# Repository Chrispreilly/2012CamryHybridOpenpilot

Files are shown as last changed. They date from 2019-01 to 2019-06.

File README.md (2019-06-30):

Got a 2018 subaru, moving the forked OP to https://github.com/c-reilly/openpilot-2012camryhybrid

# 2012 Toyota Camry Hybrid Openpilot

### Openpilot Repo

https://github.com/chrispreilly/openpilot   

### Physical Components

##### Purchased / Standard Compenents
- EON
- (Grey) Panda
- Motor Controller Board
  - See MotorControllerWiring
  
##### Customized Components Needed
- Motor Mount & Steering Wheel Mount
  - See MotorMount example, need to customize this for each car
  
### Ignition
The Panda is plugged into the OBD port, and on my Toyota the ignition pin on the panda matches with the 12V supply. As a work around I've changed in thermald to sense ignition at 13V. Battery voltage is ~12.5V, so it only senses igniton when the car is on and inverter brings the voltage up to ~13.5V.

### CAN Communication - Required Messages  
I have all messages being sent over the OBD CAN bus. As long as the steering control and safety check messages don't conflict with nything in your car, you should be able to use the OBD bus.

##### Inputs from car to openpilot:
- Blinker
- Brake Pedal
- Gas Pedal
- Wheel Speed
- Steering Angle
- Cruis Control On/Off

##### Inputs from car to Motor Controller:
- Steering Angle

##### Inputs from Openpilot to Motor Controller:
- Desired Angle

##### Inputs from Motor Controller to Openpilot:
- CAN Safety Check

### Safety
- Belt Tension should never exceed what the driver can override
- Arduino sends a CAN check message every 100ms. If openpilot doesn't hear the message for 250ms it will disengage
- If Arduino sees a gap betwwen recieving Desired Angle from Openpilot or Current Angle from the car it will turn off the motor
- If Openpilot sees a delta between current angle and desired angl of >5 degrees (meaning user override or motor lost power) it will disengage

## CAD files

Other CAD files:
MotorMount.dwg
WheelMount.dwg

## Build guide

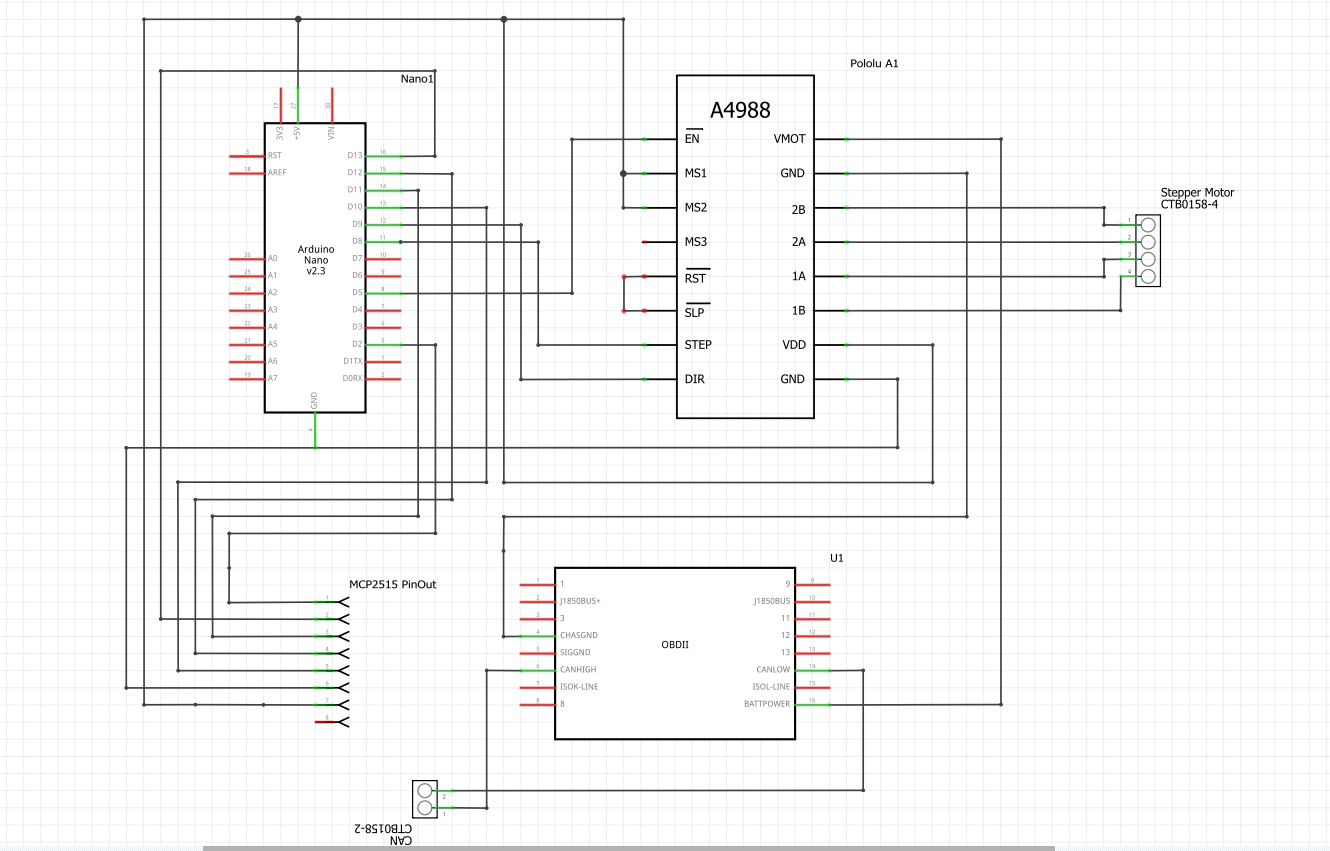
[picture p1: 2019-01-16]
MotorControllerWiring.PNG

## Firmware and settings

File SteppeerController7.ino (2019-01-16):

/*
 * Parts used
 * 
 * 1x Arduino
 * 1x MCP2515 CAN Transciever
 * 1x A4988 Stepper Driver
 * 1x NEMA17 stepper motor
 */



#include <AccelStepper.h>
#include <SPI.h>          //SPI is used to talk to the CAN Controller
#include <mcp_can.h>

//Stepper control with openpilot
//Set these variables for system config
double steerGear = 220; //steering gear diameter
double motorGear = 8; //motor gear diameter
//double angleError = 0; //degrees error needed to disengage
double microsteps = 4; //microstepping (1 = standard, 2 = half step, 4 = quarter step, 8  = eigth step)
int stepperSpeed = 2200;
int stepperAcceleration = 10000;

//set enable pin on A4988 driver
int enablePin = 5;

//init other variables
float gearRatio = 0;
float currentAngle = 0;
float desiredAngle = 0;
double lastDesiredAngle = 0;
double lastCurrentAngle = 0;
double angleDelta = 0;
double zeroAngle = 0;

long desiredStep = 0;
long lastDesiredStep = 0;
long currentStep = 0;

bool currentEngaged = false;
bool previousEngaged = false;
bool steerOverride = false;

double angleToStepFactor = 0;
double stepToAngleFactor = 0;
unsigned char len = 0;
unsigned char buf[8];
unsigned int canID;
unsigned char buf0 = 0;
unsigned char buf1 = 0;
unsigned char buf2 = 0;
unsigned char buf3 = 0;
unsigned char buf4 = 0;
unsigned char buf5 = 0;
unsigned char buf6 = 0;
unsigned char buf7 = 0;

float measure0 = 0;
float measure1 = 0;
float measure2 = 0;
float measure3 = 0;
float measure4 = 0;

int currentTime = 0;
int lastRequestTime = 0;
int lastReadTime = 0;
int lastGoToTime = 0;
int counter = 0;

float canCheck = 0;
unsigned char msg[2] = {0, 0};
int lastCANCheckTime = 0;


AccelStepper stepper(1, 8, 9); //(type(leave as 1 for a4988), step, direction)
MCP_CAN CANR(10); //CAN CS Pin



void steerCommandReceived() {
  //Serial.println("Update Received");

  //reads either 0 or 1
  buf0 = buf[0];
  currentEngaged = bitRead(buf0, 0);

  //combine 2 bufs to create big one
  buf1 = buf[1];
  buf2 = buf[2];
  measure1 = (buf1 << 8);
  measure2 = buf2;
  desiredAngle = measure1 + measure2;
  desiredAngle = desiredAngle / 100;

  lastRequestTime = millis();
  //Serial.println(desiredAngle);
  //Serial.println(currentEngaged);
  return;
}

void carAngleReceived() {

  buf0 = buf[0];
  buf1 = buf[1];
  buf4 = buf[4];
  measure0 = buf0;
  measure1 = buf1;
  measure4 = (buf4 >> 4);
  if (measure4 >= 8) {
    measure4 = -16 + measure4;
  }

  //if greater than 0, negative turn
  if (buf0 > 0) {
    currentAngle = -(384 - (measure1 * 1.5) - (measure4 / 10)); //15/16 converts to more accurate removed 15/16 because it seems more accurate to what OP is reading
  }
  else {
    currentAngle = (measure1 * 1.5) + (measure4 / 10); //15/16 converts to more accurate
  }


  //counter = counter +1;
  //Serial.println(counter);

  lastReadTime = millis();
  //Serial.print(measure1*1.5);
  //Serial.print("  ");
  Serial.println(currentAngle);
  //safetyCheck();
  return;
}

void safetyCheck() {

  return;
}

void disableLock() {
  //stepper.disableOutputs();
  //while (true){
  //delay(5000);
  //}
}

void updateDesiredStep() {

  
  angleDelta = desiredAngle - currentAngle;
  currentStep = stepper.currentPosition();

  //minus (-) because stepper is reversed direction
  desiredStep = currentStep - angleDelta * angleToStepFactor;  //currentStep + angleDelta * angleToStepFactor;
  //Serial.println(desiredStep);

//only update if reasonable change, need to determine a good number
  if (abs(lastDesiredStep - desiredStep) > 10) {

    lastDesiredStep = desiredStep;
    stepper.moveTo(desiredStep);
  }
  

  return;
}

void sendCANCheck() {

//CAN ID 500/0x1f4
  CANR.sendMsgBuf(0x1f4, 0, 2, msg);
  canCheck = canCheck + 1;
  msg[0] = canCheck;
  if (canCheck == 50)
  {
    canCheck = 0;
  }

  lastCANCheckTime = millis();

  //CANR.sendMsgBuf(0x512, 0, 2, msg); test
  //CANR.sendMsgBuf(0x513, 0, 2, msg);
  return;
}



void setup() {
  //set enable pin to disable immediately
  pinMode(enablePin, OUTPUT);
  digitalWrite(enablePin, HIGH);
  Serial.begin(115200);
  
  //Initialize CAN
RETRYCANONE:
  if (CAN_OK == CANR.begin(CAN_500KBPS))     //setting CAN baud rate to 500Kbps
  {
    Serial.println("CAN BUS Receive Shield init ok!");
    delay(5);
  }

  else
  {
    Serial.println("CAN BUS Receive Shield init fail");
    goto RETRYCANONE;
  }


//calculate system parameters
  gearRatio = motorGear / steerGear;

  stepToAngleFactor = (gearRatio) * (360 / 200) * (1 / microsteps);
  angleToStepFactor = 1 / stepToAngleFactor;

  //set stepper speed and acceleration - tune these to each system
  stepper.setMaxSpeed(stepperSpeed); //steps per second
  stepper.setAcceleration(stepperAcceleration);

  //stepper.setCurrentPosition(0);

}



/*
 * loop() updates current steering angle from the car, and desired angle from Openpilot. 
 * Based on the difference it calculates how many steps to move to achieve the desired angle and requests to move there.
 * It continues to update at 200hz as both current angle and desired angle changes.
 * Also takes advantage of the enable pin on the A4988 to disable the stepper when not engaged.
 * 
 */
void loop() {

  //Check for a new CAN message and read if angle read or request
  if (CAN_MSGAVAIL == CANR.checkReceive())
  {
    CANR.readMsgBuf(&len, buf);
    canID = CANR.getCanId();

    //If the ones we care about...
    if (canID == 0x2e4) //angle request & engaged
    {
      steerCommandReceived();
    }
    else if (canID == 0x25) //steering angle
    {
      carAngleReceived();
    }
  }



  //update MoveTo every 5 milliseconds
  currentTime = millis();
  if ((currentTime - lastGoToTime) > 5 ) { //(desiredAngle != lastDesiredAngle) && 
    //Serial.println("run");
    lastDesiredAngle = desiredAngle;
    lastGoToTime = currentTime;
    updateDesiredStep();
  }



  //enable outputs when engaged
  if (currentEngaged == true)  { // && previousEngaged == false) {
    digitalWrite(enablePin, LOW);
    previousEngaged = currentEngaged;
  }

  //disable outputs when disengaged
  else if (currentEngaged == false)  { // && previousEngaged == true) {
    digitalWrite(enablePin, HIGH);
    previousEngaged = currentEngaged;
  }



  //Time check, disable if half second passes between CAN messages
  //currentTime = millis(); //comment out to use earlier time check
  if (((currentTime - lastRequestTime) > 250) || ((currentTime - lastReadTime) > 250)) {
    currentEngaged = false;
    digitalWrite(enablePin, HIGH);
  }

  if (
    ((currentTime - lastCANCheckTime) > 100))  {
    sendCANCheck();
  }

  //check if the stepper needs to move if engaged if engaged
  if (currentEngaged == true) {

    stepper.run();
  }

} //end loop

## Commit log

2019-01-16 upload cad drawings
    [MotorMount.dwg, WheelMount.dwg]
2019-01-16 Arduino-based stepper controller
